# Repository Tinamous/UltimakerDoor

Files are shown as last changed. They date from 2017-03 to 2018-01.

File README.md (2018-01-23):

# Sliding Door for Ultimaker 2/2+

This is a set of runners that bolt to the Ultimaker 2+ so that a 3mm acrylic sheet can be used as a vertical sliding door. It does require the use of the Ultimaker bolts so may void your warranty.

The files in this folder have a 2mm gap between the desk and when the runner starts. This should be enough, but can be increased if needed with the "floorOffset" variable in OpenSCAD.

** Regular (non-extended) Ultimaker runners untested.
** Sizes other than 3mm untested.

## 3D Printed Parts

The stl files are for 3mm Acrylic. If you wish to use another thickness modify the Build.bat file (or the scad file and build manually).

Change the variable: acrylicWidth 
It should include a tollerance for your acrylic (3mm is often 3.5 in places) and a tollerance to allow it to slide (e.g. 0.5mm on the Ultimaker for PLA appears to work well), hence a 4.0 value for 3mm Acrylic.

the -Both files include both left and right for either the lower sections or the upper sections, this takes about 6 hours to print.

-Left and -Right files include individual left and right sections if you with to print them individually.

A small gap is left at the base to keep the runners clear of the desk top.

Lower sections include a stop block at the bottom to prevent the door from going below the level of the Ultimaker box which may hinder ventilation to the electronics mounted underneath the UM.

## Printer settings:
* Slicer: Cura
* Layer Height: 0.2 or 0.25
* Wall Thickness: 0.7
* Infill Density: 18%
* Speed: 60mm/s
* Supports: None
* Build Plade Adhesion: Brim (14mm)
* Nozzle: 0.4mm

## Laser Cut Parts.

A sheet of 3mm 300mm acrylic is required

Cut to the height required.

SVG file to be added when door latching is figured out.

## TimeLapse

https://www.youtube.com/watch?v=BP5jdTchPsw

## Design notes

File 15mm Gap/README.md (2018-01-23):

# Sliding Door for Ultimaker 2/2+

This is a set of runners that bolt to the Ultimaker 2+ so that a 3mm acrylic sheet can be used as a vertical sliding door. It does require the use of the Ultimaker bolts so may void your warranty.

The files in this folder have a 15mm offset from the desk to allow for feet to be placed around the ultimaker to hold it in place.

## Printer settings:

* Slicer: Cura
* Layer Height: 0.2 or 0.25
* Wall Thickness: 0.7
* Infill Density: 18%
* Speed: 60mm/s
* Supports: None
* Build Plade Adhesion: Brim (14mm)

## Laser Cut Parts.

A sheet of 3mm 300mm acrylic is required

Cut to the height required.

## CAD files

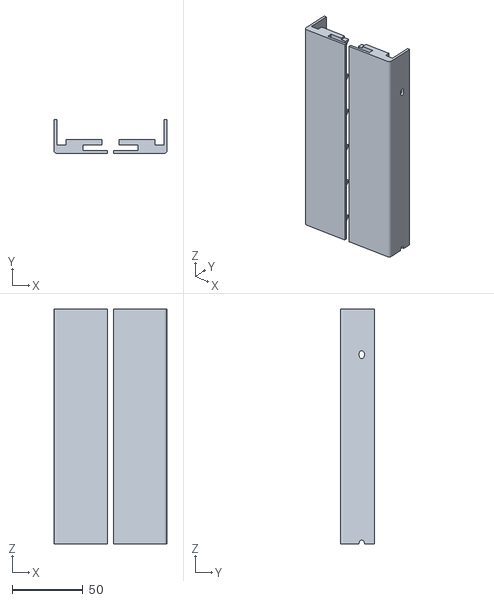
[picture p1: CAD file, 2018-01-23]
15mm Gap/UM2-Door-Upper-Both-3mm.stl
80.0 x 24.0 x 166.4

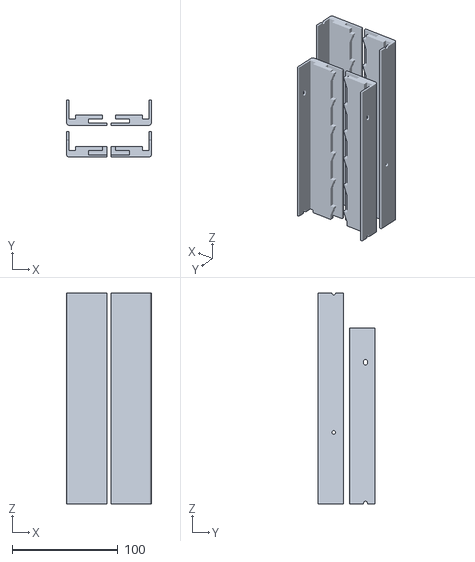
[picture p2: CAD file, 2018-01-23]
UM2-Door-All-3mm.stl
80.0 x 54.0 x 199.6

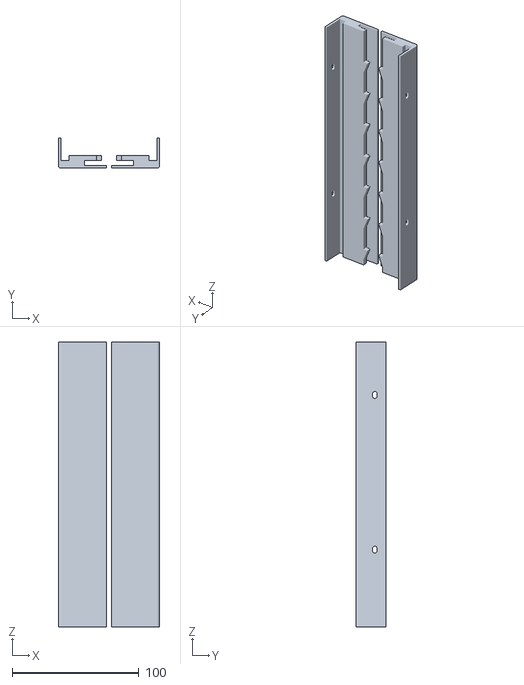
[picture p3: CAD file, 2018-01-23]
15mm Gap/UM2E-Door-Upper-Both-3mm.stl
80.0 x 24.0 x 224.8

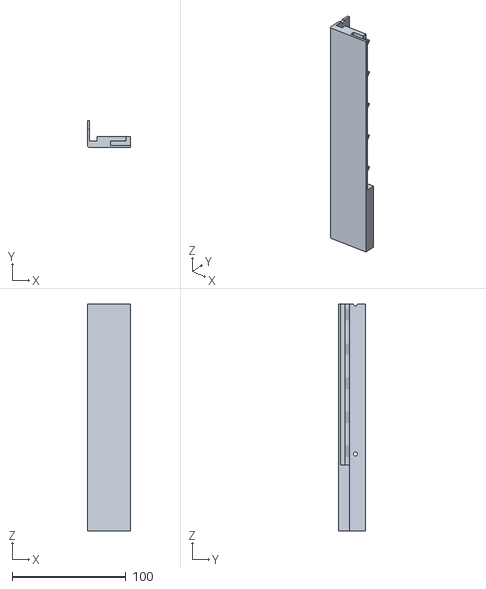
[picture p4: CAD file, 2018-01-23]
UM2-Door-Lower-Left-3mm.stl
38.0 x 24.0 x 199.6

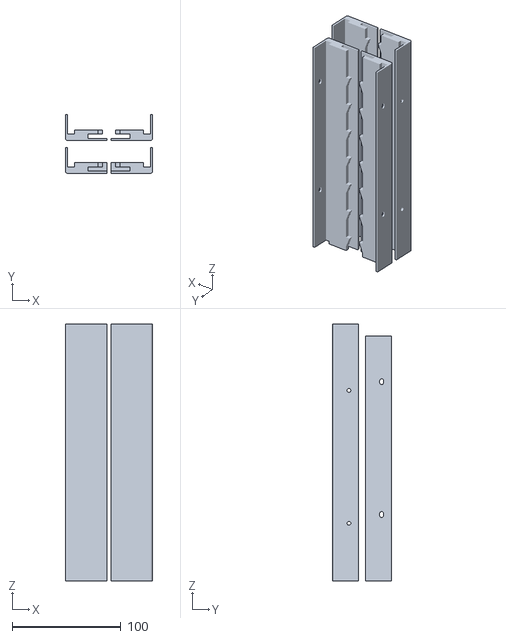
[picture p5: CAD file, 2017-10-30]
15mm Gap/UM2E-Door-All-3mm.stl
80.0 x 54.0 x 236.0

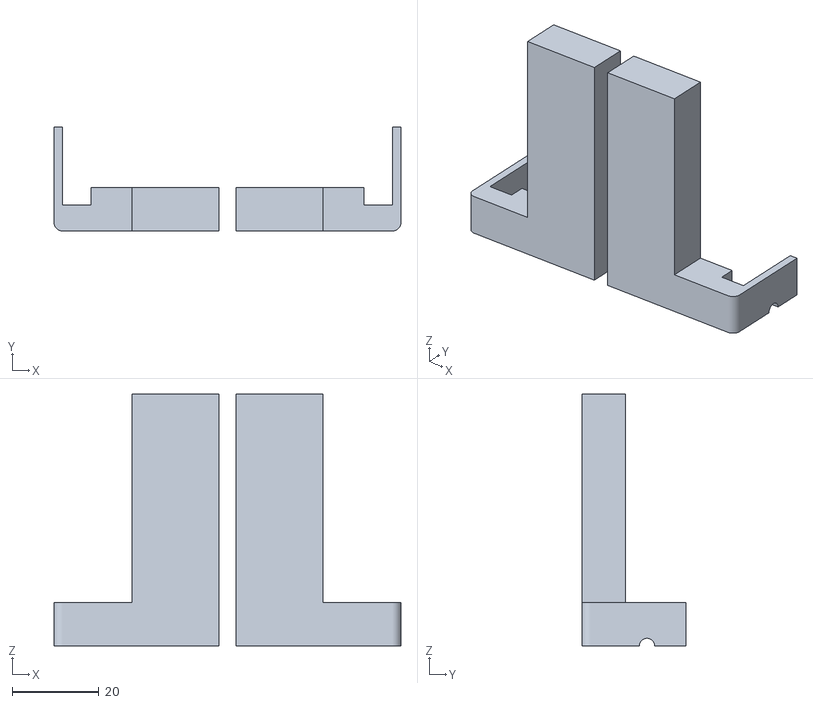
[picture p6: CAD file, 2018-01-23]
UltimakerDoorSlider-TestPiece.stl
80.0 x 24.0 x 58.0

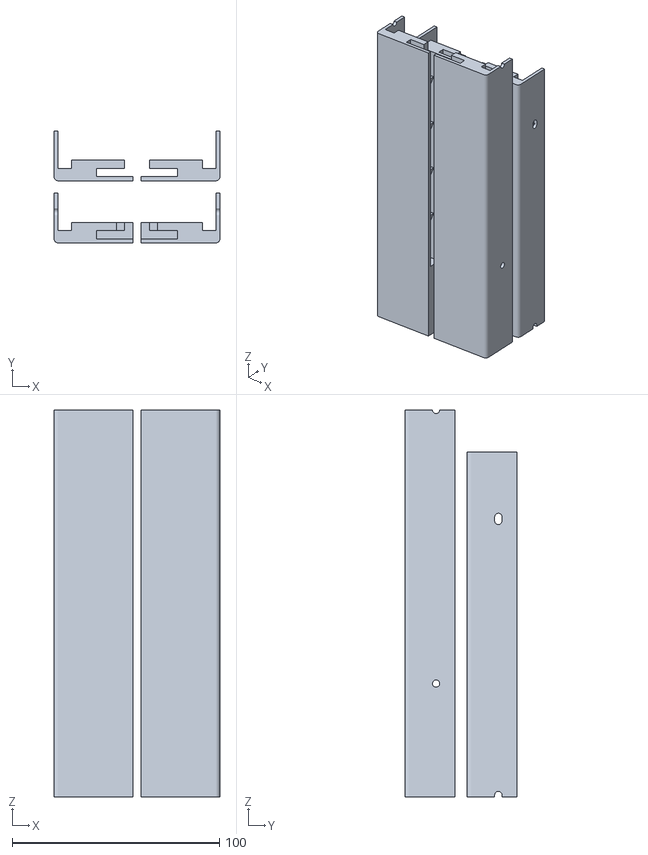
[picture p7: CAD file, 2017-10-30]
15mm Gap/UM2-Door-All-3mm.stl
80.0 x 54.0 x 186.6

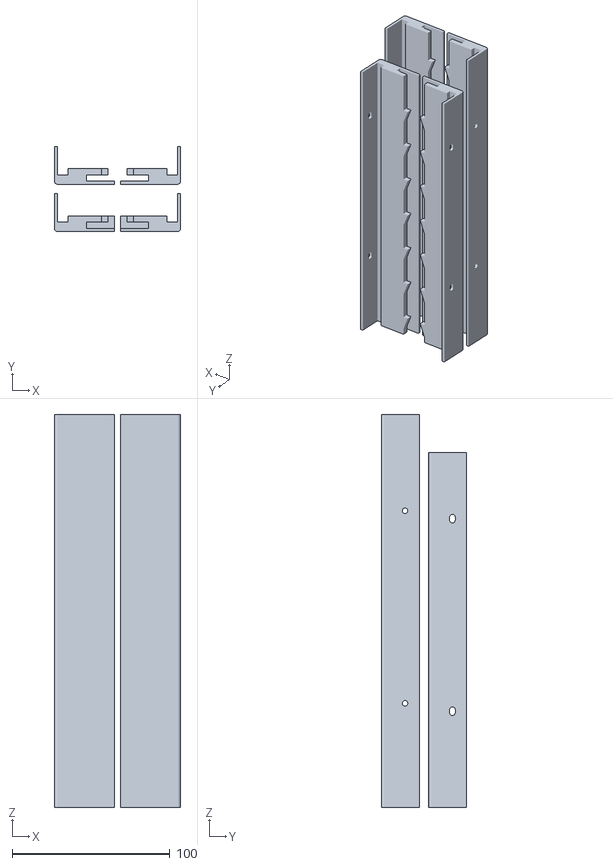
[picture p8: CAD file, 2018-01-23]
UM2E-Door-All-3mm.stl
80.0 x 54.0 x 249.0

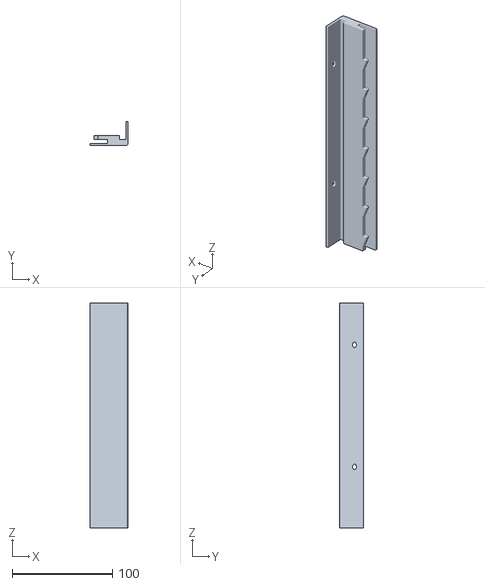
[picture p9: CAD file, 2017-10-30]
15mm Gap/UM2E-Door-Upper-Right-3mm.stl
38.0 x 24.0 x 224.8

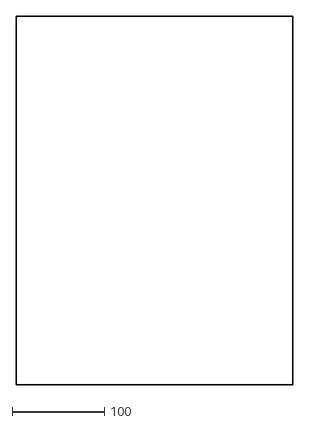
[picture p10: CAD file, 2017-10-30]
UM2E-DoorBlank.dxf
300.0 x 400.0

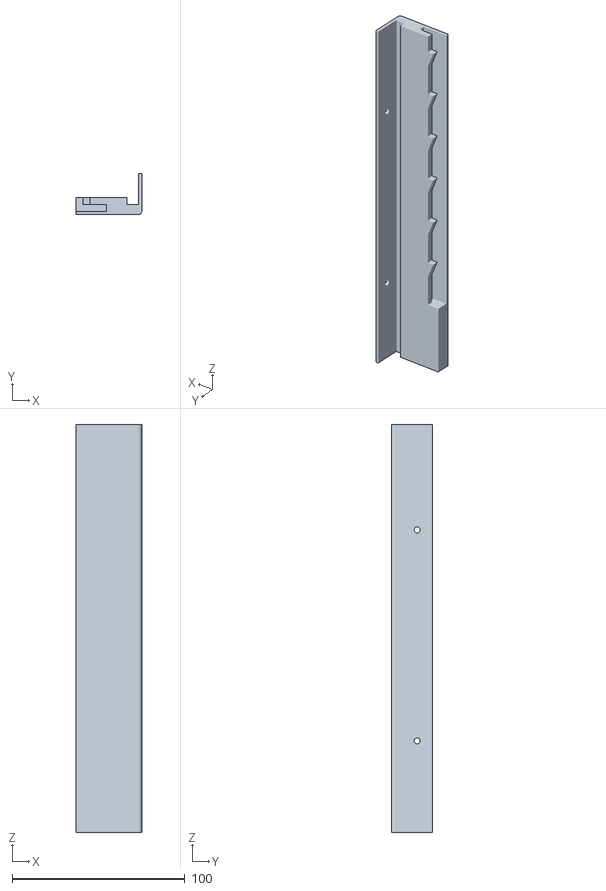
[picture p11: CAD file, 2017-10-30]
15mm Gap/UM2E-Door-Lower-Right-3mm.stl
38.0 x 24.0 x 236.0

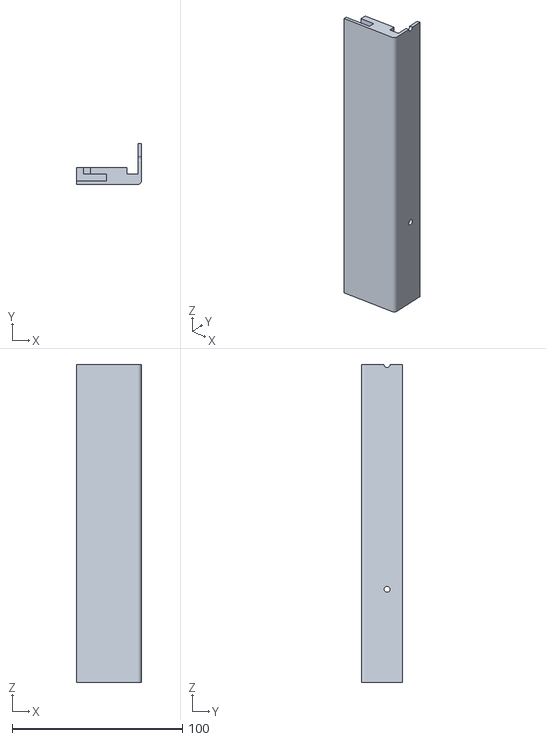
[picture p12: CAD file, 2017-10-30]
15mm Gap/UM2-Door-Lower-Right-3mm.stl
38.0 x 24.0 x 186.6

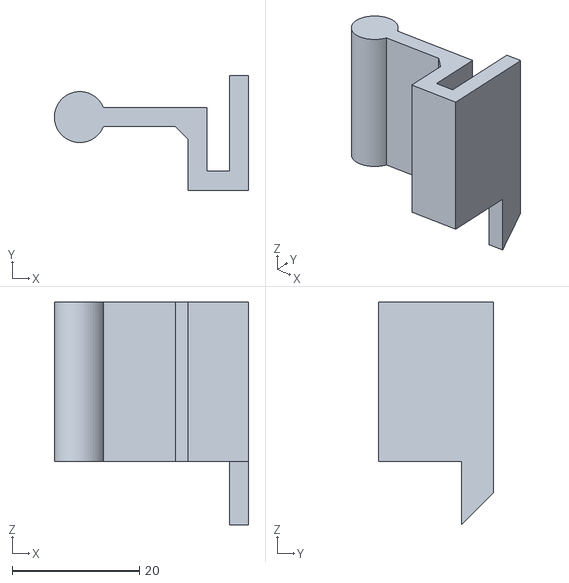
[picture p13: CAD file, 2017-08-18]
UltimakerDoorHandle-Left.stl
30.5 x 18.0 x 35.0

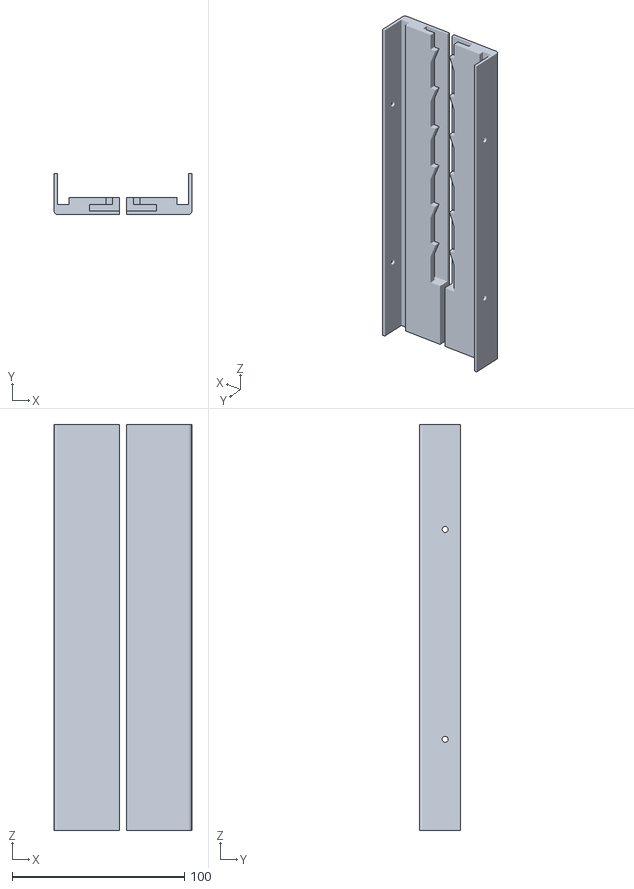
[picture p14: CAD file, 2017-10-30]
15mm Gap/UM2E-Door-Lower-Both-3mm.stl
80.0 x 24.0 x 236.0

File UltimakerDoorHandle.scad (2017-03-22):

handleLength = 25;
catchLength = 10;
acrylicWidth = 3.5;

buildLeft = false;
buildRight = false;

module handle(h) {
    linear_extrude(height = h) {         
        // 20 -> 25 gives 5mm acrylic.
        polygon(points=[[0,13],[20,13],[20,3],[20 + acrylicWidth,3],[20+acrylicWidth,18], [23+acrylicWidth,18],[23+acrylicWidth,0],[17,0],[17,8], [15,10], [0,10],[0,13]]);
        
        translate([0,11.5,0]) {
            circle(d=8, $fn=60);
        }
    }
    
    
}

module leftCatch() {
    translate([20+acrylicWidth,5,-catchLength]) {
        cube([3,1.5,catchLength]);   
    }
}

module rightCatch() {
    translate([20+acrylicWidth,5,handleLength]) {
        cube([3,1.5,catchLength]);   
    }
}

handle(handleLength);

if (buildLeft) {
    leftCatch();
}

if (buildRight) {
    rightCatch();
}

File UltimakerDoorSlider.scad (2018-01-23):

/* [Model Generation Selection] */

// Generate sliders for Ultimaker2 Extended or the regular Ultimaker2
extended = true;

// Include the lower runner halves
includeLowerSections = true;

// Include the upper runner halves
includeUpperSections = true; 

// Incldue runners for the left side of the printer
includeLeftSections = true;

// Inlude runners for the right side of the printer
includeRightSections = true;

/* [Knotches] */

// Include knotches on the inside surface to help latch the sliding door.
knotches = true;

// Spacing between knotches
knotchSpacing = 30;

/* [Model Customisation] */

// How high up the base part is filled to stop the door going all the way down. 
filledHeight = 60;
// 60mm gives just above display Actual fill is this - the floor offset

// How much speace to leave between the bottom of the runners and the floor (bottom of the UM)
//floorOffset = 15; //- if you have feet around the corners of the printer.
floorOffset = 2;

// Width of acrylic door. allow a tollerance, e.g. 3mm cast acrylic can be 3.5mm or even 4mm in places.
acrylicWidth = 4;

/* [Testing] */

// Create the test piece only. Useful for checking fit to the UM.
testPiece = false;

/* [Hidden] */

// Visualisation for UM.
ultimakerWidth = 339; 

// UM2 Extended only. 
distanceBetweenHoles = 122;

// Show the Ultimaker, door etc for model checking
includeVisualisation = false;

// Gap between models.
seperationBetweenSides = 0;
// -32 for offset in right bracked.
//seperationBetweenSides = ultimakerWidth - (38*2);
// gives 0 width for ultimaker inbeterrn
 //seperationBetweenSides = -(38*2);

module showUltimakerExtended() {
    // down 2mm as the runners are raised up by 2mm.
    translate([-(ultimakerWidth-38 +2) ,11,-2]) {
        cube([ultimakerWidth,200,490]);
        
        // Show Screws.
        translate([0,5-1,0]) {
            for (zOfffset = [69-1 : distanceBetweenHoles : 480]) {           
                translate([0,0,zOfffset]) {
                    cube([400,2,2]);
                }
            }
        }
    }
}

module showUltimakerRegular() {
    // down 2mm as the runners are raised up by 2mm.
    translate([-(ultimakerWidth-38 +2) ,11,-2]) {
        cube([ultimakerWidth,200,388]);
        
        // Show Screws.
        translate([0,5-1,0]) {
            translate([0,0,69.7]) {
                cube([400,2,2]);
            }
            translate([0,0,69.7 + 131.9]) {
                cube([400,2,2]);
            }
            translate([0,0,69.7 + 131.9 + 134.1]) {
                cube([400,2,2]);
            }    
        }
    }
}

module showDoor() {
xOffset = -(ultimakerWidth-38 +2) + 19;

    translate([xOffset ,2,15 + filledHeight-floorOffset]) {
        % cube([300,acrylicWidth,500]);
    }
}

module bracket(h) {
    linear_extrude(height = h) { 
        //+4 on the x.
        //polygon(points=[[0,0],[34,0],[34,25],[32,25],[32,7],[25.5,7],[25.5,11],[4,11],[4,8],[19,8],[19,2],[0,2], [0,0]]);
        
        difference() {
            union() {
                polygon(points=[[0,0],[36,0],[38,2],[38,20+acrylicWidth],[36,20+acrylicWidth],[36,2+acrylicWidth],[29.5,2+acrylicWidth],[29.5,6+acrylicWidth],[8,6+acrylicWidth],[8,2+acrylicWidth],[17.5,2+acrylicWidth],[17.5,2],[0,2], [0,0]]);
                
                translate([36,2,0]) {
                    // 4.2mm hole allows for a M3 pushfit nut
                    // or small cable/string run inside
                    circle(d=4, $fn=60);
                }
            }
            union() {
                translate([23,4,0]) {
                    // 4.2mm hole allows for a M3 pushfit nut
                    // or small cable/string run inside
                   // circle(d=4.2, $fn=60);
                }
            }
        }
    }
}



// Well, more take them away
module addRightKnotches(h) {
    // start at 15mm as this keeps the underside
    // vent gap in the Ultimaker open
    for (zOffset = [15: knotchSpacing: h]) {
        translate([0,6+acrylicWidth, zOffset]) {
            rotate([0,90,-90]) {
                linear_extrude(height = 4) { 
                    polygon(points=[[0,0],[10,4],[0,4],[0,0]]);
                }
            }
        }
    }
}

module addLeftKnotches(h) {
    // start at 15mm as this keeps the underside
    // vent gap in the Ultimaker open
    for (zOffset = [15: knotchSpacing: h]) {
        translate([-3,6+acrylicWidth, zOffset]) {
            rotate([0,90,-90]) {
                linear_extrude(height = 4) { 
                    polygon(points=[[10,0],[10,0],[0,4],[00,0]]);
                }
            }
        }
    }
}

module rightBracket (h)  {
    bracket(h);
    if (knotches) {
        translate([4,0,0]) {
            addRightKnotches(h);
        }
    }
}

module leftBracket (h)  {
    translate([-4,0,h]) {
        rotate([0,180,0]) {
            bracket(h);
        }
    }
    if (knotches) {
        translate([-9,0,0]) {
            addLeftKnotches(h);
        }
    }
}    

// Used by the lower section as that wants to be in a set place
module screwHole(zPosition, isBase) {
    if (isBase) {
        // Single fixed place hole
        translate([-395,0,zPosition]) {
            rotate([0,90,0]) {
                cylinder(d=3.5, h=600, $fn=20);
            }
        }
    } else {
        longScrewHole(zPosition);
    }
}

// User by the upper position to allow for a little fitting tollerance.
module longScrewHole(zPosition) {   
    // Larger hole for adjustment.
    translate([-395,0,zPosition-1]) {
        rotate([0,90,0]) {
            cylinder(d=3.5, h=600, $fn=20);
        }
    }
    
    // Join the holes.
    translate([-395,-3.6/2,zPosition-(2/2)]) {
        cube([600,3.6,2]);
    }
    
    translate([-395,0,zPosition+1]) {
        rotate([0,90,0]) {
            cylinder(d=3.5, h=600, $fn=20);
        }
    }
}

module main(h, fillBase, holes) {
    // for 2 sections to make a door on extended
    
    echo ("Height = ", h);
    echo ("First Hole At = ", holes[0]);
    
    difference() {
        union() {
            if (includeRightSections) {
                rightBracket(h);            
            }
            
            if (includeLeftSections) {
                translate([-seperationBetweenSides,0,0]) {
                   leftBracket(h);    
                }
            }
        }
        union() {
            
            translate([34-3,11+acrylicWidth,0]) {                
                // holes.
                for (holeZPosition = holes) {
                    screwHole(holeZPosition, fillBase);
                }                
            }
        }
    }   
    
    // fill the bottom(/top) to stop acrylic calling out.
    if (fillBase) {
        if (includeRightSections) {
            cube([20, 6 + acrylicWidth, filledHeight - floorOffset]);
        }
        
        if (includeLeftSections) {
            translate([-seperationBetweenSides-24,0,0]) {
                cube([20, 6 + acrylicWidth, filledHeight - floorOffset]);
            }
        }
    }
}



// Help visualise if we have the screwholes in the correct place.
module lowerSectionMarker() {
    translate([30,10,0]) {
        // first hole
        cube([10,10,70]);
        // second hole
        translate([0,10,0]) cube([10,10,70+122]);
        // top
        translate([0,20,0]) cube([10,10,70+122+61]);
    }
}

module upperSectionMarker() {
    translate([30,10,0]) {
        // first hole
        cube([10,10,61]);
        // second hole
        translate([0,10,0]) cube([10,10,61+122]);
        // top
        translate([0,20,0]) cube([10,10,61+122+61]);
    }
}

// ==============================================
// UM2 Extended runners.
// ==============================================
module extendedUpperDoorRunners() {
    // Set-up so that 2 pieced
    // can be stacked on top of each other
    
    // For upper parts.
    lowerPartHeight = (distanceBetweenHoles/2); // 122/2 == 61mm.
    
    // 28mm lower in height to so they don't jut over the top.
    // + 7.8mm takes the part to the top of the UME
    height = lowerPartHeight + (distanceBetweenHoles) + (distanceBetweenHoles/2) - 27 + 7.8; 
    
    holes = [lowerPartHeight, lowerPartHeight + distanceBetweenHoles];
    
    main(height, false, holes);
}

module extendedLowerDoorRunners() {
    // For base parts
    // actual first hole at 70mm
    // leaves 2mm gap on floor
    lowerPartHeight = 68; 
    
    height = lowerPartHeight + (distanceBetweenHoles) + (distanceBetweenHoles/2)-  floorOffset; 
    
    holes = [lowerPartHeight -  floorOffset, lowerPartHeight + distanceBetweenHoles-  floorOffset];
    
    main(height, true, holes);
}
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

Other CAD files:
UM2E-Door-Upper-Both-3mm.stl
UM2-Door-Upper-Both-3mm.stl
15mm Gap/UM2E-Door-Upper-Left-3mm.stl
UltimakerDoorHandle-Right.stl
15mm Gap/UM2-Door-Lower-Both-3mm.stl
15mm Gap/UM2-Door-Lower-Left-3mm.stl
15mm Gap/UM2-Door-Upper-Left-3mm.stl
15mm Gap/UM2-Door-Upper-Right-3mm.stl
15mm Gap/UM2E-Door-Lower-Left-3mm.stl
UltimakerDoorHandle-Simple.stl
UltimakerDoorSlider-Lower.stl

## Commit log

2017-03-22 Initial commit. -Upper.stl and -Lower.stl printed and fitted to UM2E+
    Door Handle still work in progress.
    [UltimakerDoorHandle.scad, UltimakerDoorHandle.stl, UltimakerDoorSlider-Lower.stl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]
2017-03-22 Added Build.bat to create better named .stl files.
    Updated Readme.
2017-03-22 Updated DoorHandle to allow 3.5mm for acrylic width as 3mm was too tight.
    Added variables to allow left or right version to be build by build.bat.
    [UltimakerDoorHandle.scad]
2017-03-22 Rebuild stl's with new filenames.
    [UM2-Door-Lower-Both-3mm.stl, UM2-Door-Lower-Left-3mm.stl, UM2-Door-Lower-Right-3mm.stl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]
2017-08-18 Added variables for spacing of the knotches and fill space at the bottom to prevent the door from fully closing.
    Increased knotch spacing to 30mm from 15 and filled space to prevent door covering SD card and control knob.
    [UM2-Door-Lower-Both-3mm.stl, UM2-Door-Lower-Left-3mm.stl, UM2-Door-Lower-Right-3mm.stl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]
2017-10-29 Tweaked sizings and lower part for the acrylic door to sit.
    [UM2E-Door-Lower-Both-3mm.stl, UM2E-Door-Lower-Left-3mm.stl, UM2E-Door-Lower-Right-3mm.stl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]
2017-10-30 Updated for regular sized Ultimaker2.
    UM2 doesn't have evenly spaced holes so changed how holes are generated.
    Added offset for lower section to allow for space under the guides (i.e. for feed on the ultimakers).
    Modified variable definitions to try and work with Thingiverse.
    [UM2-Door-All-3mm.stl, UM2-Door-Lower-Both-3mm.stl, UM2-Door-Lower-Left-3mm.stl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]
2017-10-30 Door outline for laser cutting for the Ultimaker Extended.
    [UM2E-DoorBlank.dxf]
2018-01-23 Improved readme.
    Rebuilt stl's with a 2mm gap between desk and the runner start, moved the ones used for Makespace to the 15mm folder as they have a 15mm gap to allow for feet around the printer.
    [UM2-Door-All-3mm.stl, UM2-Door-Lower-Both-3mm.stl, UM2-Door-Lower-Left-3mm.stl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]
